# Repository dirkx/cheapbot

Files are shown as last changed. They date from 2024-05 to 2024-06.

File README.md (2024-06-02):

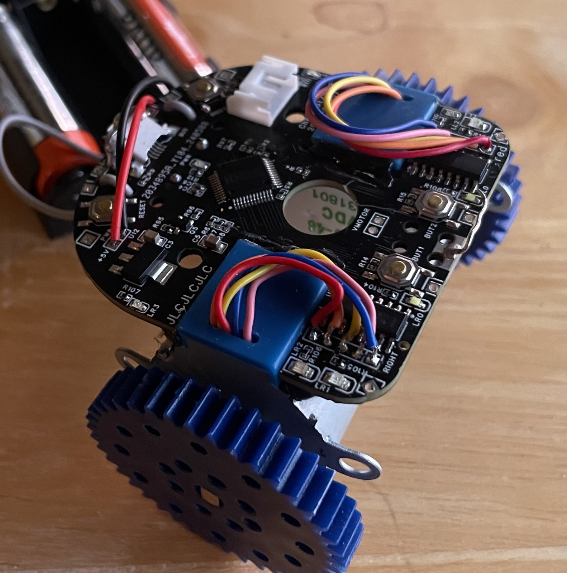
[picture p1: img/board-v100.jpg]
image of a cheapbot


A shonkbot for less than the price of a decent pint of Bristol Beer

 * Original -- http://jarkman.co.uk/catalog/robots/shonkbot.htm
 * Board -- https://oshwlab.com/dirkx/cheapbot
 * Software -- https://github.com/dirkx/cheapbot

# Preparing board 

For 1.00 boards - apply rework #0 first.

# Arduino preparation; install 

	https://github.com/DeqingSun/ch55xduino

This is done by adding the URL

	https://raw.githubusercontent.com/DeqingSun/ch55xduino/ch55xduino/package_ch55xduino_mcs51_index.json

In the settings packages list:

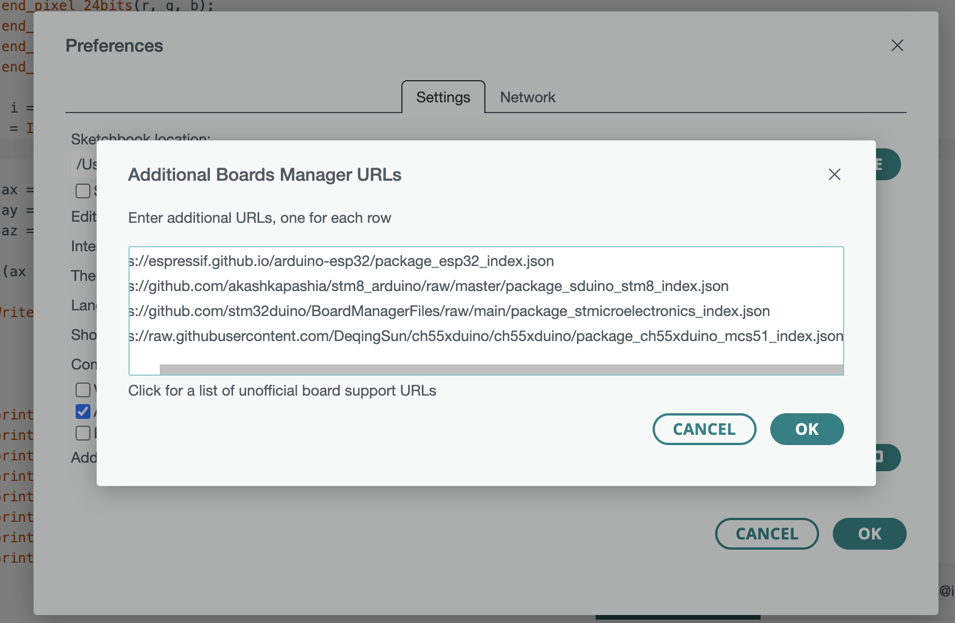
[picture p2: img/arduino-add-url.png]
image of a settings screen


Once you have done this - go to Tools and then tbe Boards, Board manager menu:

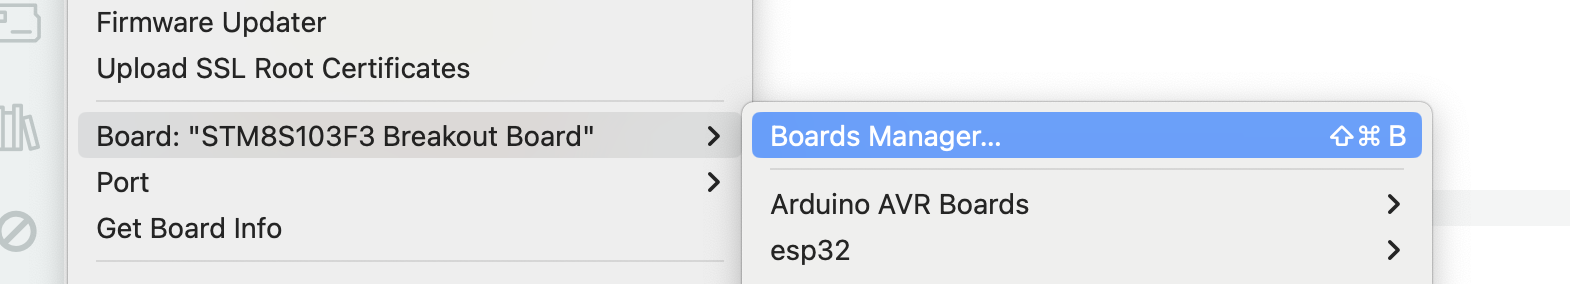
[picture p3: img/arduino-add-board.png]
image of a board manager


And search for the CH55x. Then install it:

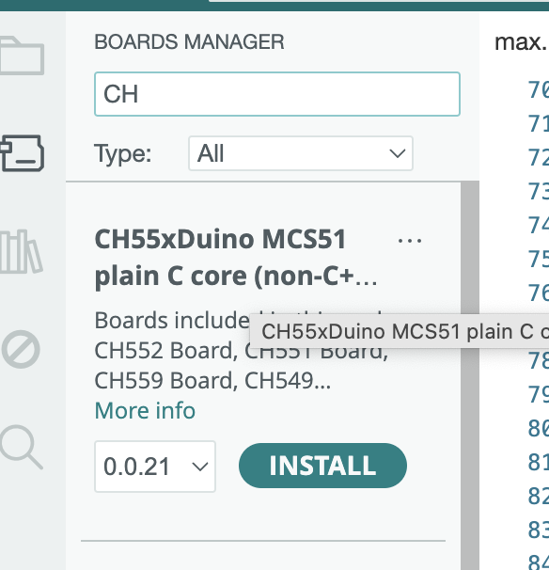
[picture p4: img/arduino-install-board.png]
image of a board instlal
.

Now search for the CH558 the 'select board' menu. If it does not appear (as shown below):

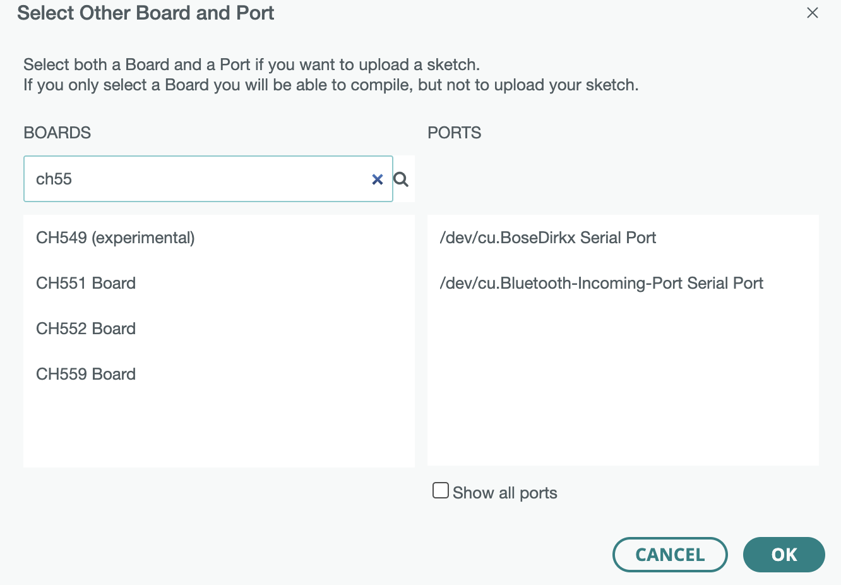
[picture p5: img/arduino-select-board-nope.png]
.

Then sadly the pull request https://github.com/DeqingSun/ch55xduino/pull/163 has not been installed. **ONLY** in this case do a manual install by

First checking out the cheapbot code to some location:

	git clone https://github.com/dirkx/cheapbot.git

And locate the file

	cheapbot/tools/arduino-ide-2.3.2-0.0.21.patch

in that bundle of files. Then go to the directory:

     cd ~/Library/Arduino15/packages/CH55xDuino/hardware/mcs51/0.0.21

And apply the patch with 

	cd ~/Library/Arduino15/packages/CH55xDuino/hardware/mcs51/0.0.21
	patch -p0 --dry-run < LOCATION_OF_ABOVE_GIT_CLONE/cheapbot/tools/ide-2.3.2-0.0.21.patch

It should show you

     patching file boards.txt
     patching file 'cores/ch55xduino/Arduino.h'
     ...

with no errors. If so - apply it again, but now for real:

	patch -p0 < LOCATION_OF_ABOVE_GIT_CLONE/cheapbot/tools/ide-2.3.2-0.0.21.patch

Then restart your arduino IDE. And you now should see a CH558 board:

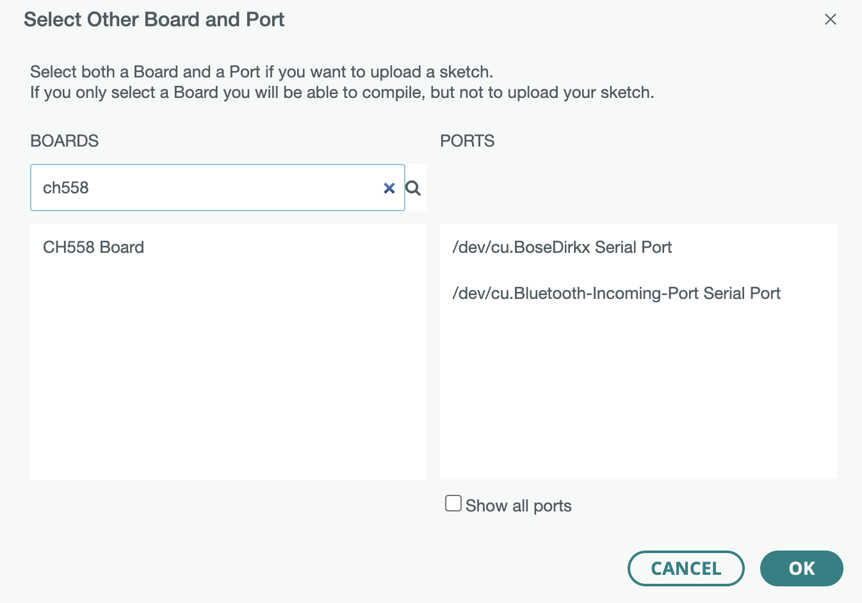
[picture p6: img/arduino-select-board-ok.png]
.

# First flashing 

	Device should be in firmware modus. If not - see Rework #1 below; then
	press boot button during insertion of USB cable.

# Later flashing #

	The standard arduino firmware will put the device in boot mode if the serial
	is set to 1200 baud shortly. So Rework #1 is not needed if your first flashing
	succeeds -and- is with an Arduino build payload.

# Manaully force into firmware boot without rework #1

Start a serial tool (e.g. SerialTools), set the baudrate to 1200 and hit the connect button. All LEDs should now come on -and serial tools should no longer see the serial device (until you flash or powercycle).

# Initial bringup #

00_blink	- check if the LEDs works. Do not connect the motors yet - they will get hot.

01_motor	- motor's wired up; pining identical as on the motor connector. 

02_buttons	- solder in buzzer (if you do it earlier - you get an annoying bzz) - button presses should now work.
		  solder jumper P0.6 needs to be in place.

# Flashing

So the CH558 is shipped from the factory with a USB bootloader. When you connect it
it should show up as 4348:55e0 (WinChipHead) on your USB bus. This signals that it
is in bootloader mode and can be flashed.

Once you have flashed it (once) from the Arduino environment - it will show up as
1209:c550 as a normal serial port. And you can see your serial println statements
here. If you set it to 1200 baud (done by selecting the right USB serial device
in the Arduino IDE) then the bootloader interprets this as a requet to go back
into boot mode. It will leave the bus; and rejoin as 4348:55e0.

If it initially shows as 1209:c550 (Generic, or Arduino) or something else,  then it has 
already been flashed. In that case it needs to be brought in BOOT mode. Depending on how 
the previous flashing went - this is either by pulling DP5.1 to the 3v3 rail; or by 
connecting P4.6 to ground during powerup.

## How to see it is ready to be flashed

When the CPU is halted & ready to be flashed; all LEDs are on; the motors
are blocked and the buzzer is buzzing (owing to all GPIO's to be high). 

## It wont flash

First check if you can get it into flash mode via the 1200 baud trick. This
requires your device to show up in the list of serial USB devices.

Use any serial tool (e.g. SerialTools); and do unplug the robot; check
the pulldown tool with the available serial ports (or screenshot it), Then
connect the robot and check again. If there is an extra port - that is
the robot. In that case - set the baudrate first to 1200; and then do
'connect' from your serial console. The device should disappear as
a serial device; and all LEDs on the robot come on. You are now in 
flashing mode - try again from your Arduino IDE to flash.

## Nope - won't flash

If this is your every first time flashing; do rework #1, press the boot button
and power up the board while holding it pressed. It now should stay in boot
mode for a few seconds. As an alternative for rework #1 - you can also touch
the leftmost pad (nearest to the buzzer) of the bootselect solder-pad on the 
back with a wire to 3v3 while powering it up. There is a 3v3 on the serial
connector.

## It still wont flash

First - check that the solderpad on the back is to 'boot'.

Secondly - check in the Arduino IDE that you selected "Bootloader Pin": "PD5.1 (USB DP to 3V2)"
and not to P4.6. As that will break the Arduino Flashing `1200 baud serial' trick.

## Darn - I did select 4.6 by accident (and 1200 baud does not work)

You will need to pul PP4.6 down during powerup to GND. An easy way to do this is to
touch the leftmost pin (furthest away from Led LR2 and the board edge) of R106. There
is a convenient ground pad in the middle top of the board - between button 1 and 2.

# Board Version 1.00

The side with the CPU (big square chi) is the top side.

Hold the board with the USB connector nearest to you - and the side with Vmotor
away from you. So the USB cable becomes the 'tail'. And the two white LEDs (LR0
and LL0) become the 'headlights' at the front. 

## Rework #0 

The slot for the USB connector was not cut out properly. As a result the
USB connector is at a 45 degree angle. Secure it by soldering a U shapped
piece of stuff wire over it - thus fixing it in position. And then put some
extra solder on the rear 2 tabs. 

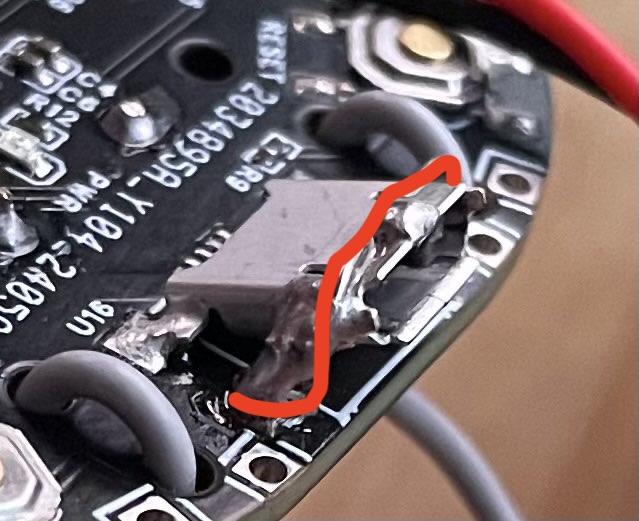
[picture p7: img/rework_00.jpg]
rework 0, bridge over the USB connector


## Rework # 1 

This rework is not essential; provided your very first download is done
from the Arduino IDE environment; so that it has the '1200 baud' trick
to get the device into boot-state.

The BOOT switch should have been wired to 3V3; it was wired by accident
to GND. Remove R10 and cut the trace at the back of the board that runs
to the pin-header below R10. Then place a bodge wire from the
left R10 pad (i.e. away from the BOOT switch, 3V3), to the top right
pin of the BOOT switch (nearest to the USB connector). 
	
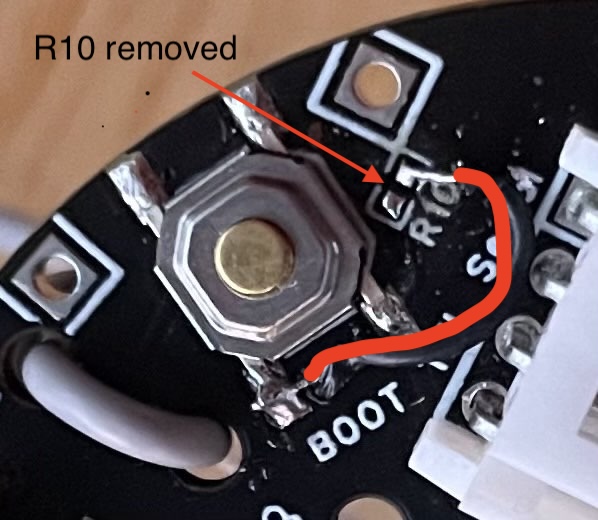
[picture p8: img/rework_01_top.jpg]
rework 01 - remove R10, add bodge wire on top side of board

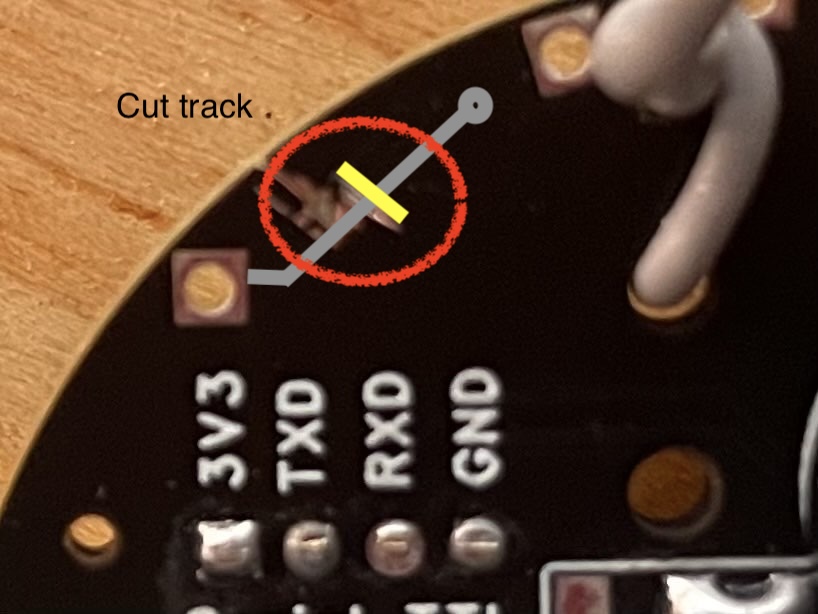
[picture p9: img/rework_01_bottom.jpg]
rework 01 - cut trace bottom board


# Bill of materials

| Item | Source | Price |
|---|---|---|
| 3 AA batteriess | some local shop | 3.00 euro per 3 |
| PCB including parts and soldering| JLCPCB | 2.10 euro/piece at 25 units FOR |
| 2 28byj-48  Steppers | Aliexpres | 0.80-1.90 euro per pair, inc. shipping |
| 3AA Battery nest | Amazon | 0.82 euro/piece inc. shipping |
| Some stiff wire or tie-wraps |||
| A pen |||
| Bit of tape to make the pen the right thickness |||
| Some hotglue |||

## Known flaws of 1.00

 *  The connector are 2mm rather than 2.54mm spaced; so standard motors cannot use their (too long) cables and connectors. They have to be soldered in or to be given a new connector. The pitch is a bit fine for a beginner. The PCB needs to be made about 5mm bigger in every direction to accomdate this.

 * The hole in the middle is a bit small for the `thick' sharpie pent.

 * The batterynest mounting holes need a rethink; with short bolts they obscure the hole of the pen -and- the nuts are a bit fiddly `under' the motor.

 * The motor voltage is not well labeled (top missing)

 * The solder jumper for boot/0.6 is not as nice as the one for the motor; a smaller one should be selected.

 * The battery connector should be one size bigger (it is now more the size common on LiPo -- as opposed to 3 AA or 3 AAA nests).

 * Easier D4.6 pad near GND for alternative boot.

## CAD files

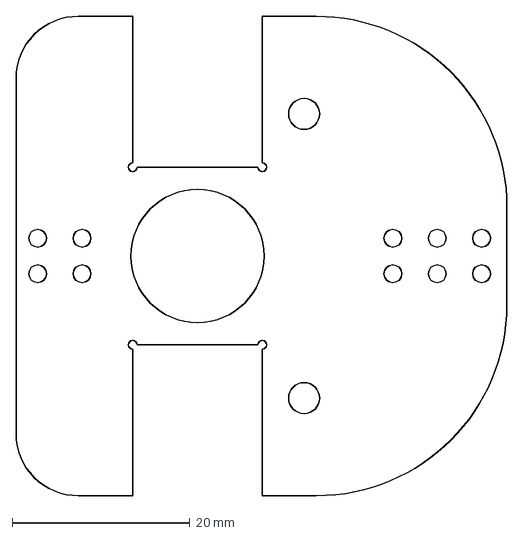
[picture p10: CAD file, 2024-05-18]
dxf/sheep3.dxf
55.3 x 54.0 mm

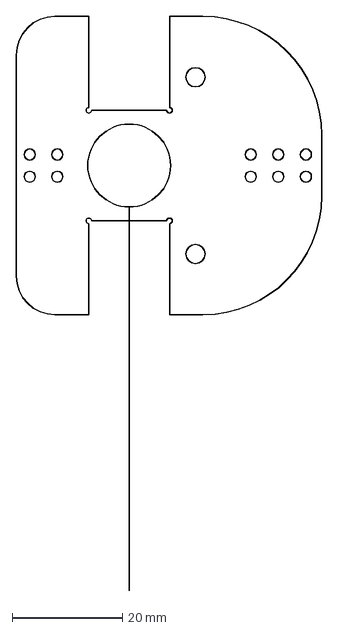
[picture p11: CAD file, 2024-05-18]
dxf/sheep2.dxf
55.3 x 103.9 mm

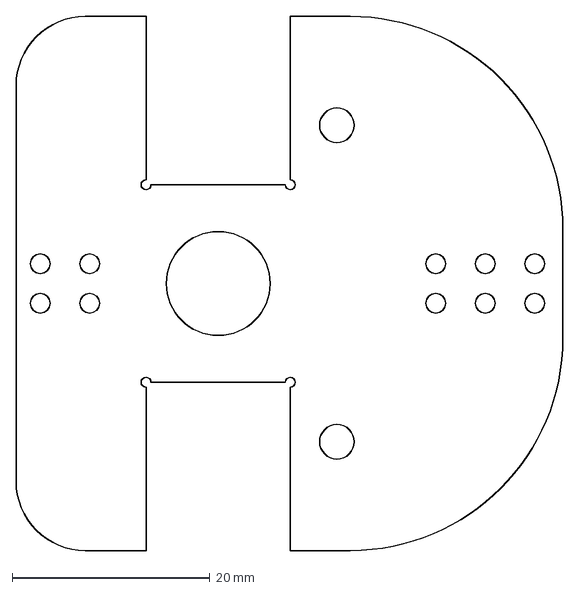
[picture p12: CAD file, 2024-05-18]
dxf/view.dxf
55.3 x 54.0 mm

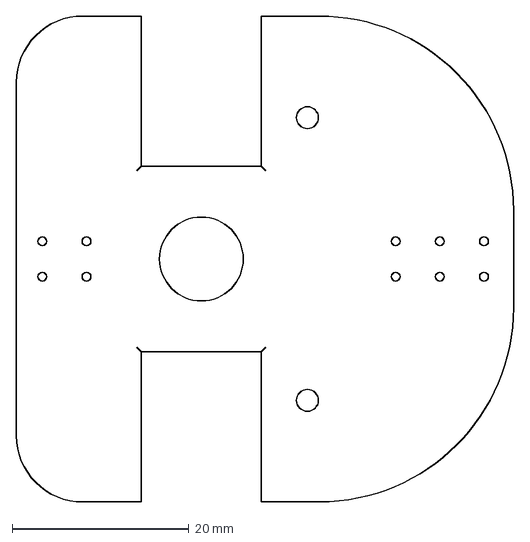
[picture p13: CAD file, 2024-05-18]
dxf/cut.dxf
56.3 x 55.0 mm

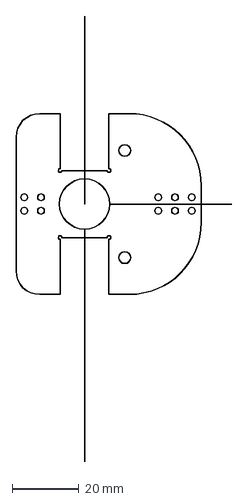
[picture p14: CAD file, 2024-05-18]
dxf/sheep.dxf
64.4 x 133.0 mm

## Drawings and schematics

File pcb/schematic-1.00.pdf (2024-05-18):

Reviewed

Drawn

VER

Create Date
Part Number
PAGE | OF

Schematic

Update Date

SIZE

Page

# cheapbot

2024-05-13

# 2024-05-06 cheapbot-CH555L

## Version history

# EasyEDA.com

## EasyEDA

V0.1 | A4

## JLCPCB-002 EasyEDA

2.01
Changed connector to another type with more quantity. Moved type text down to not clash with hole.
Fix labels and remove pins from BOM
Increase resistors LEDs to 510

2.00 - submitted to fab 2024/05/06 as bb8f688029634c50b28ee354019839c5_1715027231000_Y96

2.02
Fixed clearance around hole
2.03
Stressed/added doc line for USB cutout

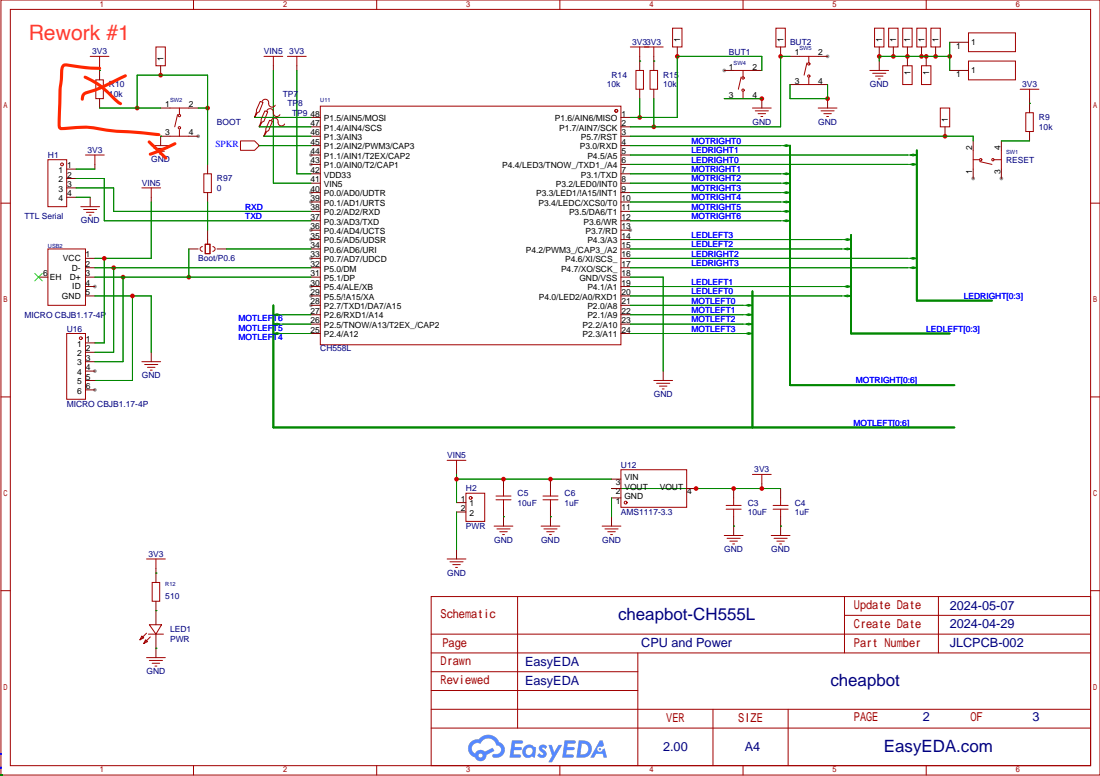
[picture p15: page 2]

P2.3/A11 24 P2.4/A12 25 P2.5/TNOW/A13/T2EX_/CAP2 26 P2.6/RXD1/A14 27 P2.7/TXD1/DA7/A15 28 P5.5/!A15/XA 29 P5.4/ALE/XB 30 P5.1/DP 31 P5.0/DM 32 P0.7/AD7/UDCD 33 P0.6/AD6/URI 34 P0.5/AD5/UDSR 35 P0.4/AD4/UCTS 36 P0.3/AD3/TXD 37 P0.2/AD2/RXD 38 P0.1/AD1/URTS 39 P0.0/AD0/UDTR 40 VIN5 41 VDD33 42 P1.0/AIN0/T2/CAP1 43 P1.1/AIN1/T2EX/CAP2 44 P1.2/AIN2/PWM3/CAP3 45 P1.3/AIN3 46 P1.4/AIN4/SCS 47 P1.5/AIN5/MOSI 48

# 7C 10 6C 11 5C 12 4C 13 3C 14 2C 15 1C 16

# GNDLEDRIGHT3

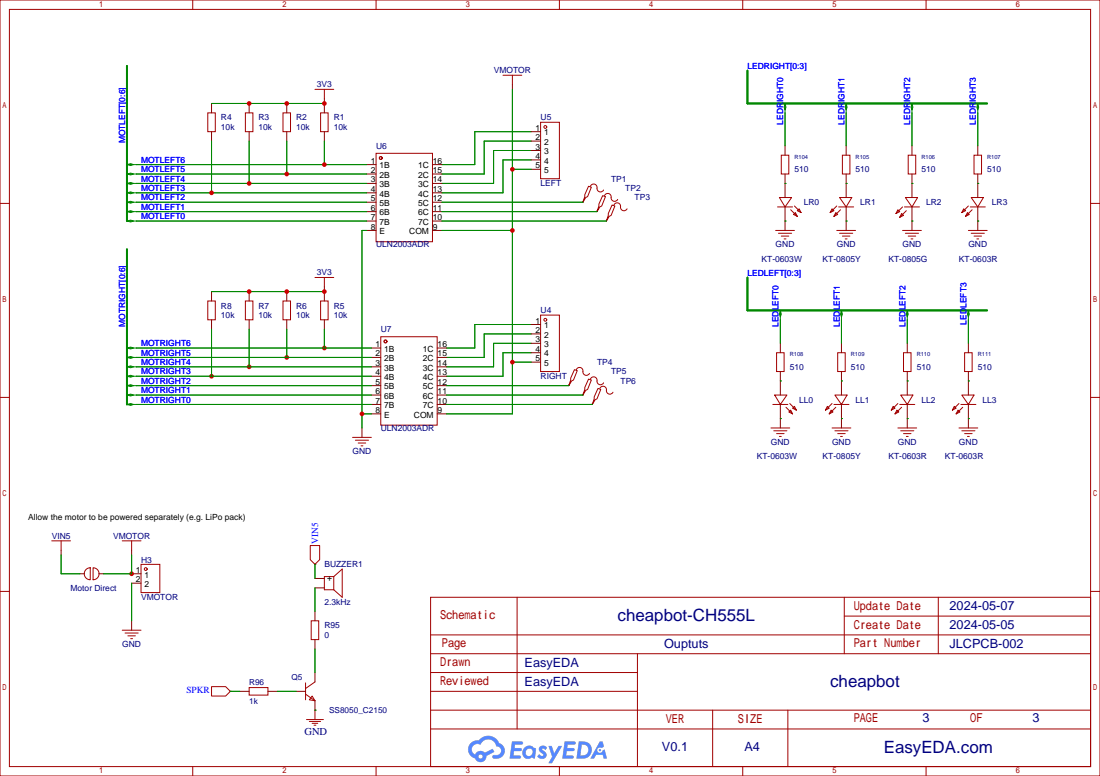
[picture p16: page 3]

Allow the motor to be powered separately (e.g. LiPo pack)
VIN5

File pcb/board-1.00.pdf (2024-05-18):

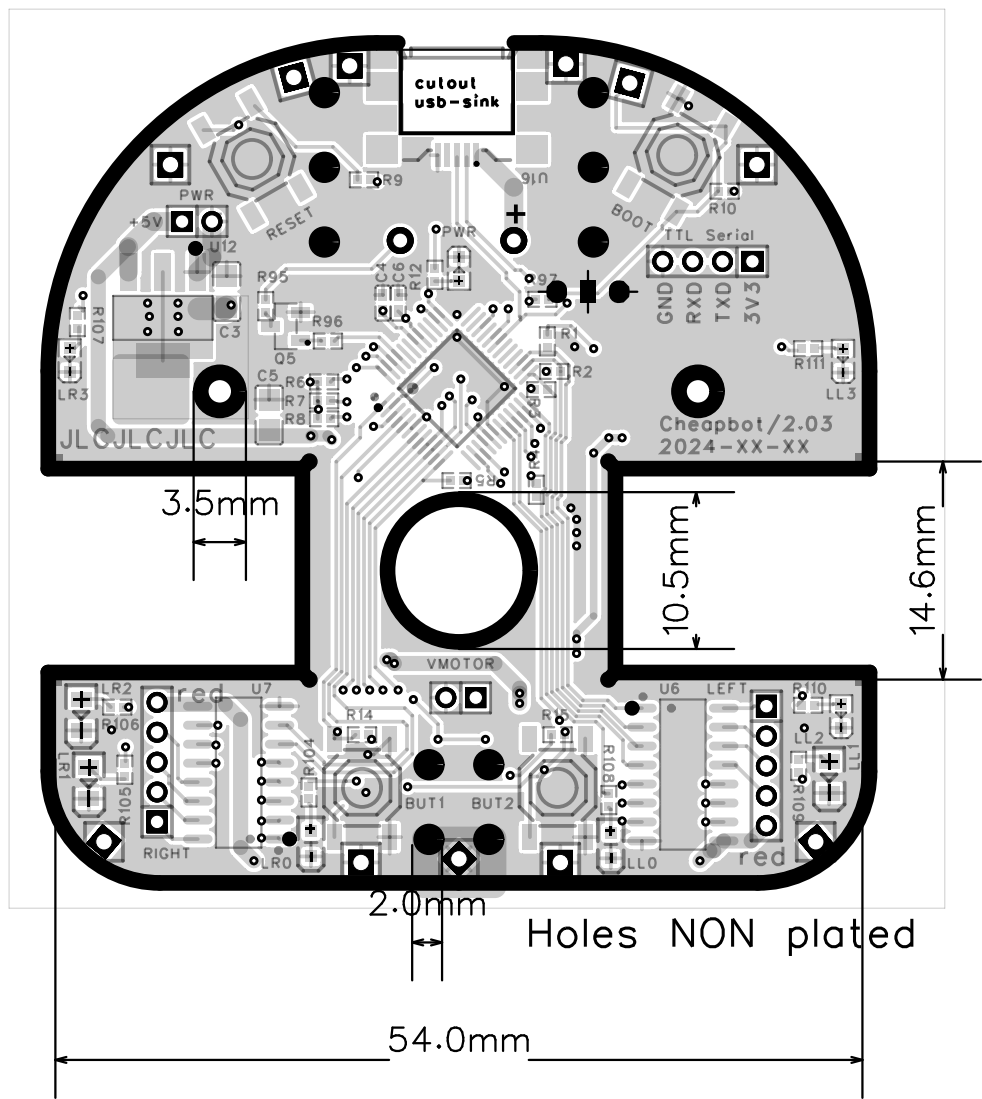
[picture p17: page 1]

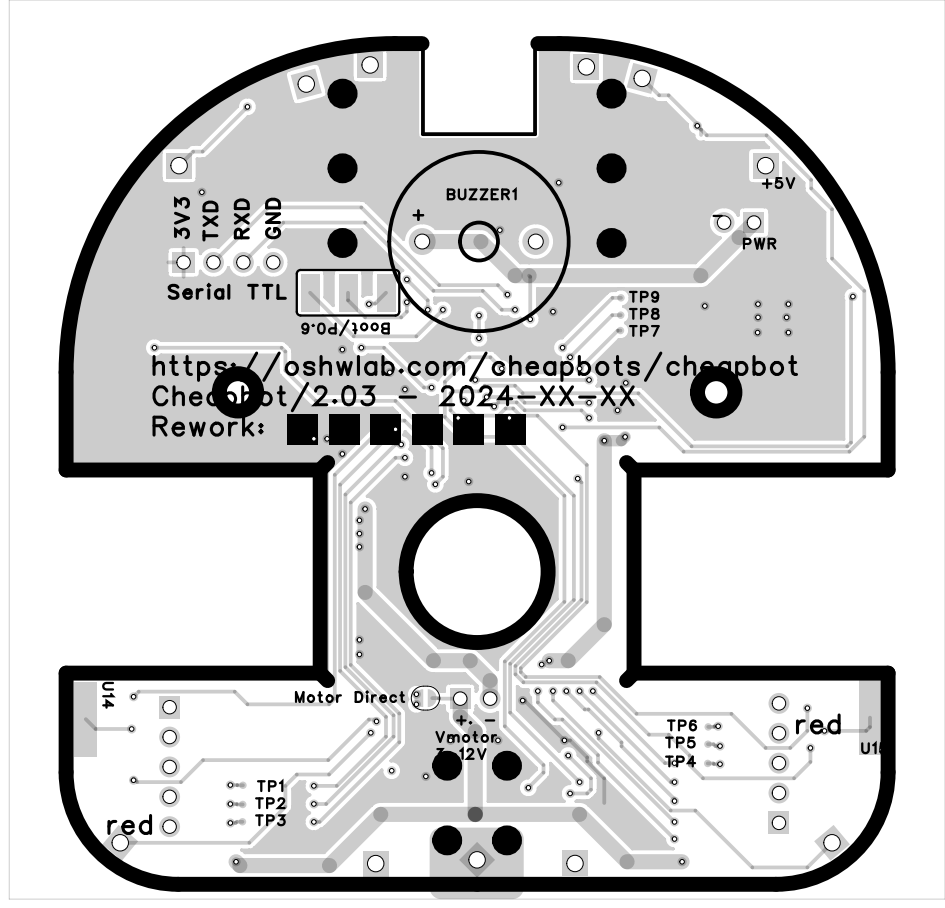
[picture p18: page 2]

Rework: Cheapbot/2.03 - 2024-XX-XX https://oshwlab.com/cheapbots/cheapbot

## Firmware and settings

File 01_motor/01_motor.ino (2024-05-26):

/* CH559 selected
     Bootloader P5.1 (USB D+) - pullup
*/

#define LL0 (40 + 0) // Led left 0, P4.0 - white (on front)
#define LL1 (40 + 1) // Led left 1, P4.1 - yellow/orange
#define LL2 (40 + 2) // Led left 2, P4.2 - red (port side)
#define LL3 (40 + 3) // Led left 3, P4.3 - red (on back)

#define LR0 (40 + 4) // Led right 0, P4.4 - white (on front)
#define LR1 (40 + 5) // Led right 1, P4.5 - yellow/orange
#define LR2 (40 + 6) // Led right 2, P4.6 - green (star board)
#define LR3 (40 + 7) // Led right 3, P4.7 - red (on back)

uint8_t led_right[4] = { LR0, LR1, LR2, LR3 };
uint8_t led_left[4] = { LL0, LL1, LL2, LL3 };

void led_init() {
  for (int i = 0; i < 4; i++) {
    pinMode(led_left[i], OUTPUT);
    digitalWrite(led_left[i], LOW);

    pinMode(led_right[i], OUTPUT);
    digitalWrite(led_right[i], LOW);
  }
}

// Motor - red is middel for H/V coils
//
#define MOTORLEFT0 (20) // TP 1 (back of board)
#define MOTORLEFT1 (21) // TP 2
#define MOTORLEFT2 (22) // TP 3
#define MOTORLEFT3 (23) // orange - coil 1 (V, rev)
#define MOTORLEFT4 (24) // yellow - coil 3 (H, rev)
#define MOTORLEFT5 (25) // pink - coil 2 (V, pos)
#define MOTORLEFT6 (26) // blue - coil 4 (H, pos)

// Motor - red is middel for H/V coils
//
#define MOTORRIGHT0 (30) // TP 6
#define MOTORRIGHT1 (31) // TP 5
#define MOTORRIGHT2 (32) // TP4 
#define MOTORRIGHT3 (33) // orange - coil 1 (V, rev)
#define MOTORRIGHT4 (34) // yellow - coil 3 (H, rev)
#define MOTORRIGHT5 (35) // pink - coil 2 (V, pos)
#define MOTORRIGHT6 (36) // 

const unsigned int stepsPerRevolution = 2038;

// pinout both motors
//
const uint8_t MOTOR_LEFT = 0;
const uint8_t MOTOR_RIGHT = 1;

const uint8_t MOTOR_GPIO[2][4] = {
  {MOTORLEFT3, MOTORLEFT4, MOTORLEFT5, MOTORLEFT6},
  {MOTORRIGHT3, MOTORRIGHT4, MOTORRIGHT5, MOTORRIGHT6}
};

const uint8_t STEP_PATTERN[] = {0b0001, 0b011, 0b0010, 0b0110, 0b0100, 0b1100, 0b1000, 0b1001};
uint8_t motor_state[2] = { 0, 0 };

void motor_gpio(uint8_t *p, uint8_t v)
{
  for (int i = 0; i < 4; ++i)
    digitalWrite(p[i], (v & (1 << i)) ? HIGH : LOW );
}

void motor_set(uint8_t motor, uint8_t v)
{
  if (motor_state[motor] == v) {
    motor_gpio(MOTOR_GPIO[motor], 0);
    return;
  };

  motor_gpio(MOTOR_GPIO[motor], STEP_PATTERN[v & 0x7]);
  motor_state[motor] = v;
}

void motor_step(uint8_t motor, int dir) {
  motor_set(motor, (motor_state[motor] + dir + 4) & 7);
}

void motor_init() {
  for(int i = 0; i < 50; i++) 
      digitalWrite(i, LOW);

  digitalWrite(led_right[0], HIGH);

#if 0
  pinMode(MOTORRIGHT0, OUTPUT);
  pinMode(MOTORRIGHT1, OUTPUT);
  pinMode(MOTORRIGHT2, OUTPUT);
  pinMode(MOTORRIGHT3, OUTPUT);

  digitalWrite(MOTORRIGHT0, LOW);
  digitalWrite(MOTORRIGHT1, LOW);
  digitalWrite(MOTORRIGHT2, LOW);
  digitalWrite(MOTORRIGHT3, LOW);

  digitalWrite(MOTORRIGHT0, HIGH);
  delay(300);
  digitalWrite(MOTORRIGHT0, LOW);
  digitalWrite(MOTORRIGHT1, HIGH);
  delay(300);
  digitalWrite(MOTORRIGHT1, LOW);
  digitalWrite(MOTORRIGHT2, HIGH);
  delay(300);
  digitalWrite(MOTORRIGHT2, LOW);
  digitalWrite(MOTORRIGHT3, HIGH);
  delay(300);
  digitalWrite(MOTORRIGHT3, LOW);

  digitalWrite(led_right[0], LOW);
#endif

  for (uint8_t i = 0; i < 2; ++i) {
    for (uint8_t j = 0; j < 4; ++j)
      pinMode(MOTOR_GPIO[i][j], OUTPUT);
    motor_gpio(MOTOR_GPIO[i], 0);
  };

#if 1
  // Wiggle all motors.
  for (uint8_t j = 0; j < 4; ++j) {
    digitalWrite(led_left[j], HIGH);
    digitalWrite(MOTOR_GPIO[0][j], HIGH);
    digitalWrite(MOTOR_GPIO[1][j], HIGH);
    delay(300);
    digitalWrite(led_left[j], LOW);
    digitalWrite(MOTOR_GPIO[0][j], LOW);
    digitalWrite(MOTOR_GPIO[1][j], LOW);
    delay(300);
  };
#endif
}

void setup() {
  led_init();
  motor_init();
  for (int i = 0; i < 4; i++)
    digitalWrite(led_right[i], LOW);
  for (int i = 0; i < 4; i++)
    digitalWrite(led_left[i], LOW);
}

// the loop function runs over and over again forever
int i = 0;
void loop() {
  digitalWrite(led_left[0] , !digitalRead(led_left[0]));

  motor_step(MOTOR_LEFT, 1);
  motor_step(MOTOR_RIGHT, 1);
  delay(5);
}

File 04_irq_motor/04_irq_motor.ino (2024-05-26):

#define CHEAPBOT

/* using 28BYj - 48 motors from http://www.ebay.co.uk/itm/131410728499 */

#define STEPS_PER_REV (4096.0 / 2.0) /* these motore come in two different gear rations, \
                                       * see http://42bots.com/tutorials/28byj-48-stepper-motor-with-uln2003-driver-and-arduino-uno/ 
                                       * and http://forum.arduino.cc/index.php?topic=71964.15
                                       */

#define MAX_SPEED 350         // 800 is a sensible limit on 5v motor supply, 300 is a sensible limit on 3v.
#define MAX_ACCELERATION 400  // 1600 on 5v, 400 on 3v

#define WHEEL_DIAMETER 48.0  // radius of your wheel in mm
#define WHEEL_SPACING 150.0  // distance from one wheel to the other in mm

#ifdef CHEAPBOT
#include <Stepper.h>
Stepper(leftStepper, STEPS_PER_REV, 8, 9, 10, 11);
Stepper(rightStepper, STEPS_PER_REV, 8, 9, 10, 11);
#else
#include <AccelStepper.h>

// Define a stepper and the pins it will use
AccelStepper leftStepper(AccelStepper::FULL4WIRE, 2, 4, 3, 5);  // note middle two pins are swapped to work with 28BYJ-48
                                                                // wire arduino pin D2 to driver board IN1, and so on

AccelStepper rightStepper(AccelStepper::FULL4WIRE, 6, 8, 7, 9);  // note middle two pins are swapped!
#endif

#ifndef CHEAPBOT
// Current position in mm, assuming we started pointing up the Y axis
float currentX = 0.0;
float currentY = 0.0;
float currentDirection = 0.0;  // in radians clockwise from the Y axis
#endif

typedef struct movement {
  int turn;
  int distance;
} movement;
#define MAX_MOVEMENTS 40


#ifndef CHEAPBOT
void goToXY(float x, float y);
#endif
void go(float distance);
void turn(float degrees);

movement movements[MAX_MOVEMENTS];

int nextMovement = 0;
boolean doneTurn = false;
boolean doneDistance = false;
int numMovements = 0;

void doNextMovement() {

  if (doneTurn && doneDistance) {
    doneTurn = false;
    doneDistance = false;
    nextMovement++;
  }

  if (nextMovement >= numMovements)
    return;  // finished


  if (!doneTurn) {
    doneTurn = true;
    turn(movements[nextMovement].turn);
  } else if (!doneDistance) {
    doneDistance = true;
    go(movements[nextMovement].distance);
  }
}

void addMovement(float turn, float distance) {
  if (numMovements >= MAX_MOVEMENTS)
    return;

  movements[numMovements].turn = turn;
  movements[numMovements].distance = distance;
  numMovements++;
}

inline void buildMovements() {
  // S
  addMovement(90, 40);
  addMovement(-90, 40);
  addMovement(-90, 40);
  addMovement(90, 40);
  addMovement(90, 40);

  addMovement(0, 10);

  //h
  addMovement(90, 80);
  addMovement(180, 40);
  addMovement(90, 40);
  addMovement(90, 40);

  addMovement(-90, 20);

  //o
  addMovement(0, 40);
  addMovement(-90, 40);
  addMovement(-90, 40);
  addMovement(-90, 40);
  addMovement(-90, 40);

  addMovement(0, 20);

  //n
  addMovement(-90, 50);
  addMovement(180, 10);
  addMovement(-90, 40);
  addMovement(90, 40);

  addMovement(-90, 20);

  //k
  addMovement(-90, 80);
  addMovement(180, 40);
  addMovement(-135, 40);
  addMovement(180, 40);
  addMovement(-90, 40 * 1.414);

  addMovement(-45, 20);

  //y
  addMovement(-90, 40);
  addMovement(180, 40);
  addMovement(-90, 40);
  addMovement(-90, 40);
  addMovement(180, 80);
  addMovement(90, 20);
}

void setup() {

#ifndef CHEAPBOT
  leftStepper.setMaxSpeed(MAX_SPEED);              // 800 is a sensible limit on 5v motor supply, 300 is a sensible limit on 3v.
  rightStepper.setMaxSpeed(MAX_SPEED);             // 800 is a sensible limit on 5v motor supply, 300 is a sensible limit on 3v.
  leftStepper.setAcceleration(MAX_ACCELERATION);   // 1600 on 5v
  rightStepper.setAcceleration(MAX_ACCELERATION);  // 1600 on 5v
#endif

  buildMovements();
#ifndef CHEAPBOT
  doNextMovement();
#endif
}

void loop() {
#ifdef CHEAPBOT
  doNextMovement();
#else
  if (leftStepper.distanceToGo() == 0 && rightStepper.distanceToGo() == 0)
    doNextMovement();

  leftStepper.run();
  rightStepper.run();
#endif
}

float stepsForDistance(float distance) {
  return distance * STEPS_PER_REV / (3.1415 * WHEEL_DIAMETER);
}


#ifndef CHEAPBOT
void goToXY(float x, float y) {
  float distance = sqrt((x - currentX) * (x - currentX) + (y - currentY) * (y - currentY));

  float theta = atan2((y - currentY), (x - currentX)) - currentDirection;
}
#endif

void go(float distance) {
  float steps = stepsForDistance(distance);
#ifndef CHEAPBOT
  leftStepper.setCurrentPosition(0);
  rightStepper.setCurrentPosition(0);
  leftStepper.move(steps);
  rightStepper.move(-steps);
#else
  leftStepper_step(-steps);
  rightStepper_step(-steps);
#endif

#ifndef CHEAPBOT
  currentX += distance * sin(currentDirection);
  currentY += distance * cos(currentDirection);
#endif
}

void turn(float degrees)  //  clockwise
{
  float theta = radians(degrees);
  float distance = WHEEL_SPACING * 0.5 * theta;
  float steps = stepsForDistance(distance);
#ifdef CHEAPBOT
  leftStepper_step(-steps);
  rightStepper_step(-steps);
#else
  leftStepper.setCurrentPosition(0);
  rightStepper.setCurrentPosition(0);
  leftStepper.move(-steps);
  rightStepper.move(-steps);
  currentDirection += theta;
#endif
}

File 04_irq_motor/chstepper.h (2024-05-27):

const uint32_t stepsPerRevolution = 2038;
const uint32_t distancePerRevolution = 140;  // millimeter (~d x PI)
const uint16_t maxSpeed = 300;               // mm/second
const uint16_t speedAcc = 300;               // mm/second/second -- go to topspeed in 1 second.
const uint16_t tocksPerSecond = 3000;        // 5kHz stepping speed (max, just above max speed)
const uint16_t accAdjustTock = 50;
const uint16_t speedInc = speedAcc * accAdjustPerSecond / tocksPerSecond;

// https://www.instructables.com/BYJ48-Stepper-Motor/
////   step 0 1 2 3 4 5 6 7 
// red.     - - - - - - - -  common
// orange   x x           x 
// yellow     x x x
// pink           x x x 
// blue               x x x
const uint8_t STEP_PATTERN[] = { 0b0001, 0b011, 0b0010, 0b0110, 0b0100, 0b1100, 0b1000, 0b1001 };
const uint8_t STOP_PATTERN = 0xb000;

typedef struct {
  uint32_t steps_to_take;
  uint16_t steps;
  uint8_t speed;
  uint8_t portbase;
  uint16_t skip;
  uint8_t portbase;
  uint8_t flags;
} motor;

#define INREVERSE(x) ((x)->flags & 1)

motor left = { .portbase = 23 }, right = { .portbase 33 };

static volatile uint32_t tocks = 0;

void initMotor(motor* m, uint8_t portBase) {
  m->steps_to_take = 0;
  m->steps = 0;
  m->speed = 0;
  m->portbase = portBase;
  m->skip = 1;
}

void stepMotor(motor* m) {
  // Early exit when there is nothing to do or
  // if it is not our time yet.
  //
  if (!m->steps_to_take)
    return;

  // stop the motor when we're done
  if (m->steps_to_take == 0) {
    m->steps_to_take = 0;
    m->skip = 1;
    m->portbase &= 0xF0 + STOP_PATTERN;
    return;
  };

  if (0 == tocks % m->skip) {
    // take a step
    uint8_t at = m->steps & 7;
    if (INREVERSE(m))
      at = 7 - at;
    m->portbase &= 0xF0 + STEP_PATTERN[at];
    m->steps++;
  };

  // See if it is time to adjust acceleration
  if (0 == tocks % accAdjustPerSecond) {

    // See if we need to change speed.
    if (m->steps < m->steps_to_take / 2) {
      if (m->speed > maxSpeed)
        return;

      // We are not yet at the halfway point. Allow to go faster
      //
      m->speed += speedInc;
      if (m->speed > maxSpeed)
        m->speed = maxSpeed;
    } else {
      // We're past the halfway point - slow down at the tail end
      //
      if (m->speed > speedInc * (m->steps_to_take - m->steps)) )
      return;

      m->speed -= speedInc;
      if (m->speed < 1)
        m->speed = 1;
    }
    // Update the time/skip
    m->skip = 1024 / m->speed;
  }
}

void irq() {
  tocks++;
  stepMotor(&left);
  stepMotor(&right);
}

void moveMm(motor* m, int distInMm) {
  if (distInMm < 0) {
    distInMm = -distInMm;
    m->flags |= 1;
  } else {
    m->flags &= ~1;
  };
  m->steps_to_take = distInMm / distancePerRevolution * stepsPerRevolution;
}

#define isMoving() (left.steps_to_take || right.steps_to_take)

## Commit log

2024-05-18 First cut at cheapbots that have just arrived from JLCPCB
    [cut.dxf, sheep.dxf, sheep2.dxf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]
2024-05-19 add irq timer example -- needs patch in main.c (see https://github.com/DeqingSun/ch55xduino/issues/165
    [03_irq_timer.ino]
2024-05-20 Add BOM
2024-05-20 Fix BOM
2024-05-26 irq drivern stepper
2024-05-27 tweaks stepper
